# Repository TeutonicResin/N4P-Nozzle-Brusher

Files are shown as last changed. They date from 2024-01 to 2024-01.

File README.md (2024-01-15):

# N4P-Nozzle-Brusher

 N4P Nozzle Cleaning Solution

Beim Elegoo Neptune 4 Pro erfolgt die Messung des Z-Offsets sehr nah an der Druckbettoberfläche. Dies kann dazu führen, dass Verunreinigungen an der Düse schnell zu fehlerhaften systemseitig gemessenen Z-Offsets führen. Eventuell vorhandener Materialrückstand bewirkt, dass das Bett während der Offset-Messung nach unten gedrückt wird, wodurch der gemessene Abstand zu hoch ist. Dies führt dazu, dass die Düse zu nah am Bett liegt. Die Ausprägung dieses Effekts wird durch die Härte und Menge des Rückstands beeinflusst.

Da ich nicht auf automatisiertes Bettleveling (KAMP) vor jedem Druck verzichten möchte, habe ich einen Ansatz für ein automatisiertes Reinigungssystem entworfen.

Du benötigst lediglich eine Bürste, das Makro und eine Anpassung in deinem Start-Print-Makro. Außerdem habe ich eine No-Go-Area (Polygon) für den Orca-Slicer erstellt, damit diese nicht genutzt wird.

Die Bürste habe ich von Amazon (<https://www.amazon.de/dp/B0CHNZ458F>) bezogen und den Bürstenkopf nach 40 mm am Griff abgetrennt. Du kannst auch jede halbwegs passende andere Bürste verwenden. Das parametrisierte Fusion360-Modell, eine Step-Datei sowie die STL-Datei werden bereitgestellt.

#### Installation ####

Drucke die Halterung aus hitzebeständigem Material (ABS, ASA, ...).
Setze die Bürste in die Halterung ein.
Befestige die Halterung an der vorderen linken Ecke des Druckbetts.
Kopiere das Makro (**macro.cfg**) in deine **printer.cfg**.

Füge folgende Zeile in dein Start-Makro nach dem Aufheizen des Bettes und vor dem Bettleveling ein: `CLEAN_NOZZLE EXTRUDER_TEMP={params.EXTRUDER_TEMP|default(200)|float} WIPES={10}`.
(Parameter WIPES: Anzahl der Reinigungsbewegungen (Standardwert = 10).
Reinigungstemperatur = Extrusionstemperatur - 40°C.)

Optional: Füge unter Druckereinstellungen -> ausgenommene Druckbettfläche im Orca-Slicer das folgende Polygon hinzu: `0x0,25x0,25x5,5x5,5x42,0x42`.

Dein N4P sollte nun vor jedem Bettleveling seine Düse reinigen und hoffentlich anschließend einen korrekten Z-Offset liefern.

Viel Spaß!

---

As the Z-offset measurement on the Elegoo Neptune 4 Pro occurs very close to the print bed surface, contaminants on the nozzle can quickly lead to inaccuracies in the system-measured Z-offset. Any existing material residue causes the bed to be pressed down during the offset measurement, resulting in a higher measured distance. This, in turn, positions the nozzle too close to the bed. The severity of this effect is influenced by the hardness and quantity of the residue.

Since I don't want to forgo automated bed leveling (KAMP) before each print, I've devised an approach for an automated cleaning system.

All you need is a brush, the macro, and an adjustment in your Start-Print-Macro. Additionally, I've created a No-Go-Area (Polygon) for the Orca Slicer to avoid its usage.

I sourced the brush from Amazon (https://www.amazon.de/dp/B0CHNZ458F) and cut the brush head after 40mm from the handle. You can also use any reasonably fitting alternative brush. The parameterized Fusion360 model, a Step file, and the STL file are provided.

#### Installation: ####

Print the holder in a heat-resistant material (ABS, ASA, ...).
Insert the brush into the holder.
Attach the holder to the front left corner of the print bed.
Copy the macro (**macro.cfg**) into your **printer.cfg**.

Add the following line to your Start-Macro after heating the bed and before bed leveling: `CLEAN_NOZZLE EXTRUDER_TEMP={params.EXTRUDER_TEMP|default(200)|float} WIPES={10}`.
(Parameter WIPES: Number of cleaning movements (default = 10).
Cleaning temperature = Extrusion temperature - 40°C.)

Optional: Add the following polygon under Printer Settings -> Excluded Print Bed Area in the Orca Slicer: `0x0,25x0,25x5,5x5,5x42,0x42`.

Your N4P should now clean its nozzle before each bed leveling and hopefully deliver a correct Z-offset afterward.

Enjoy!

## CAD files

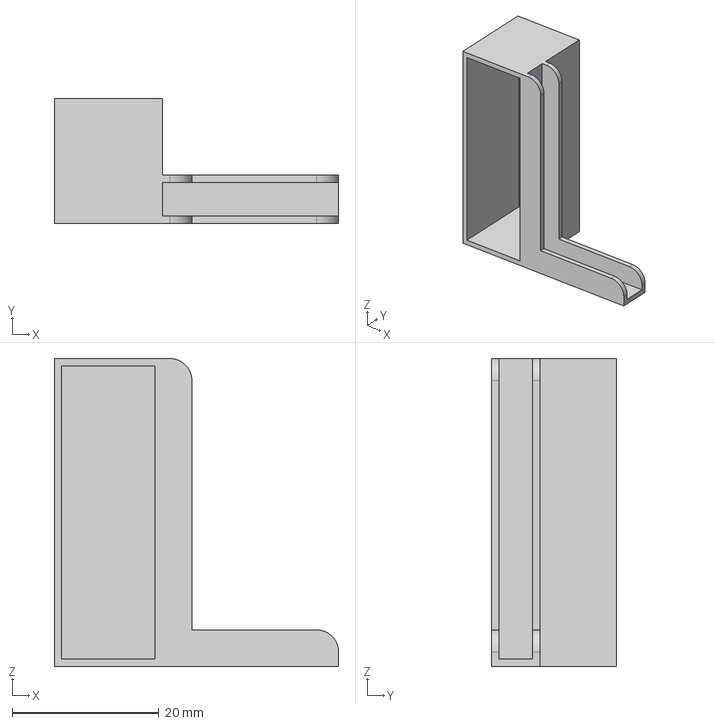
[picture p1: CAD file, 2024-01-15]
Step/N4P-Nozzle Brusher.step
38.8 x 17.0 x 42.0 mm

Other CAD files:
STL/BrushClip.stl
Fusion360/N4P-Nozzle Brusher.f3d

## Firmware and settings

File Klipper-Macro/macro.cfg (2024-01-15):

#######################################################################
## Clean Nozzle
#######################################################################
[gcode_macro clean_nozzle]
gcode:
  {% set LOWERED_EXTRUDER_TEMP = params.EXTRUDER_TEMP|default(180)|int-40 %}
  {% set WIPES = params.WIPES|default(10)|int %}
  #Position the nozzle
  G90
  G0 X-10 Y20 Z10 F5000
  #Heat up nozzle to extruder temperature - 40°C
  {action_respond_info("Clean nozzle: Heating up to {}°C the do {} wipes.".format(
    (LOWERED_EXTRUDER_TEMP),
    (WIPES)
  ))}
  M109 S{LOWERED_EXTRUDER_TEMP}
  #Bring the nozzle down
  G0 Z4
  #Swing the nozzle
  {% for wipe in range(WIPES) %}
      G0 Y5 F3000
      G0 Y35 F3000
  {% endfor %}
  #Bring the nozzle up
  G0 X-10 Y20 Z10 F5000
  # Home to get the correct offset
  G28
